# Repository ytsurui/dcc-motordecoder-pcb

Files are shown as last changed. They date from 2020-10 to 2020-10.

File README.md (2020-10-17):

# Atmel ATtiny45 DCC Decoder PCB Data

NMRA規格の信号を受信して作動する、モーター駆動専用のDCCデコーダーのDCCデコーダの基板設計データです。

主にNゲージ鉄道模型への搭載を想定して小型に設計してあります。

主要回路についてはすべてディスクリートで構成してあるため、[回路図](docs/schematic.pdf)を参考にして、ブリッジダイオード、MOSFETなどを適宜大電流に対応可能な部品に差し替えることで、より大型のゲージに対応できるデコーダを構成できるかもしれません。

回路図、基板設計データ、面付け済みの設計データを含みます。
<br>面付け済みのデータについては、ガーバーデータも含みます。 (elecrowにて製造できることを確認済み)

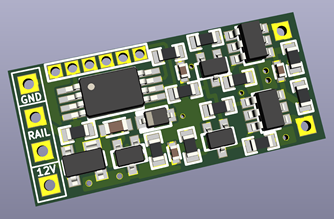
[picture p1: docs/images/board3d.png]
PCB 3D Preview

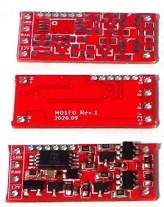
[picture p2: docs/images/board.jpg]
PCB


### 主要スペック
  * 組み立て後の基板サイズ: 22mm x 10mm x 1.7mm
  * 推奨最大電圧: 16V (搭載する鉄道模型車両の最大電圧以下で使用してください)
  * 出力電流: 最大0.5A
  * コンデンサの搭載や、室内灯電源に対応する+12V / GNDのランドを用意
  * マイコン書き込み用端子を用意し、実装後のプログラム書き換えも可能<br>(AVR ISPのピンを1.27mmピッチで1列に伸ばしています)

### 閲覧・編集に必要なCAD (開発環境)
  * KiCad Version (5.1.6)-1 (またはそれ以降)

### 対応するファームウェア
  * [Atmel ATtiny45 DCC Decoder Firmware](https://github.com/ytsurui/dcc-motordecoder-firmware)

### 各種ドキュメント
  * [パーツリスト](docs/partslist.md)

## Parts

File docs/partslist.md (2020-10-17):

# Parts List

<table>
  <tr>
    <td>Reference</td>
    <td>Name</td>
    <td>Package</td>
    <td>Count</td>
    <td>Shop Links</td>
  </tr>
  <tr>
    <td>U1</td>
    <td>ATTiny45-20XUR</td>
    <td>TSSOP-8</td>
    <td>1</td>
    <td><a href="https://www.digikey.jp/product-detail/ja/microchip-technology/ATTINY45-20XUR/ATTINY45-20XURCT-ND/2774364">Digikey (ja)</a><br />
    <a href="https://www.digikey.jp/product-detail/en/microchip-technology/ATTINY45-20XUR/ATTINY45-20XURCT-ND/2774364">Digikey (en)</a></td>
  </tr>
  <tr>
    <td>D1</td>
    <td>BAS3007A-RPP</td>
    <td>SOT-143</td>
    <td>1</td>
    <td><a href="https://www.digikey.jp/product-detail/ja/infineon-technologies/BAS3007ARPPE6327HTSA1/BAS3007ARPPE6327HTSA1CT-ND/2023144">Digikey (ja)</a><br />
    <a href="https://www.digikey.jp/product-detail/en/infineon-technologies/BAS3007ARPPE6327HTSA1/BAS3007ARPPE6327HTSA1CT-ND/2023144">Digikey (en)</a></td>
  </tr>
  <tr>
    <td>D3</td>
    <td>UDZV5.1B</td>
    <td>SOD-323</td>
    <td>1</td>
    <td><a href="https://www.digikey.jp/product-detail/ja/rohm-semiconductor/UDZVTE-175-1B/UDZVTE-175-1BCT-ND/4571455">Digikey (ja)</a><br />
    <a href="https://www.digikey.jp/product-detail/en/rohm-semiconductor/UDZVTE-175-1B/UDZVTE-175-1BCT-ND/4571455">Digikey (en)</a><br />
    <a href="https://akizukidenshi.com/catalog/g/gI-07434/">秋月電子通商</a></td>
  </tr>
  <tr>
    <td>Q1, Q2</td>
    <td>DMG6601LVT<br>DMG6602SVTQ<br>FDC6333</td>
    <td>SOT-23-6</td>
    <td>2</td>
    <td><a href="https://www.digikey.jp/product-detail/ja/diodes-incorporated/DMG6601LVT-7/DMG6601LVT-7DICT-ND/3677910">Digikey, DMG6601LVT (ja)</a><br />
    <a href="https://www.digikey.jp/product-detail/en/diodes-incorporated/DMG6601LVT-7/DMG6601LVT-7DICT-ND/3677910">Digikey, DMG6601LVT (en)</a><br>
    <a href="https://www.digikey.jp/product-detail/ja/diodes-incorporated/DMG6602SVTQ-7/DMG6602SVTQ-7DICT-ND/5176059">Digikey, DMG6602SVTQ (ja)</a><br>
    <a href="https://www.digikey.jp/product-detail/en/diodes-incorporated/DMG6602SVTQ-7/DMG6602SVTQ-7DICT-ND/5176059">Digikey, DMG6602SVTQ (en)</a><br>
    <a href="https://www.digikey.jp/product-detail/ja/on-semiconductor/FDC6333C/FDC6333CCT-ND/965584">Digikey, FDC6333 (ja)</a><br>
    <a href="https://www.digikey.jp/product-detail/en/on-semiconductor/FDC6333C/FDC6333CCT-ND/965584">Digikey, FDC6333 (en)</a>
    </td>
  </tr>
  <tr>
    <td>Q3, Q4, Q5</td>
    <td>2SC4116-GR</td>
    <td>SC-70</td>
    <td>3</td>
    <td><a href="https://www.digikey.jp/product-detail/ja/toshiba-semiconductor-and-storage/2SC4116-GR-LF/2SC4116-GRLFCT-ND/3191333">Digikey (ja)</a><br />
    <a href="https://www.digikey.jp/product-detail/en/toshiba-semiconductor-and-storage/2SC4116-GR-LF/2SC4116-GRLFCT-ND/3191333">Digikey (en)</a><br />
    <a href="https://akizukidenshi.com/catalog/g/gI-02705/">秋月電子通商</a></td>
  </tr>
  <tr>
    <td>C1, C3, C6</td>
	  <td>0.1uF 25V 1005</td>
	  <td>1.0mm x 0.5mm</td>
	  <td>3</td>
    <td><a href="https://www.digikey.jp/product-detail/ja/murata-electronics/GRM155R71H104KE14J/490-13342-1-ND/5973352">Digikey (ja)</a><br />
    <a href="https://www.digikey.jp/product-detail/en/murata-electronics/GRM155R71H104KE14J/490-13342-1-ND/5973352">Digikey (en)</a><br />
    <a href="https://akizukidenshi.com/catalog/g/gP-13377/">秋月電子通商</a></td>
  </tr>
  <tr>
    <td>C2</td>
    <td>22uF 6.3V 1608</td>
    <td>1.6mm x 0.8mm</td>
    <td>1</td>
    <td><a href="https://www.digikey.jp/product-detail/ja/murata-electronics/GRM188R60J226MEA0D/490-7611-1-ND/4280544">Digikey (ja)</a><br />
    <a href="https://www.digikey.jp/product-detail/en/murata-electronics/GRM188R60J226MEA0D/490-7611-1-ND/4280544">Digikey (en)</a><br />
    <a href="https://akizukidenshi.com/catalog/g/gP-08062/">秋月電子通商</a></td>
  </tr>
  <tr>
    <td>R1</td>
    <td>100kohm 1/10W 1608</td>
    <td>1.6mm x 0.8mm</td>
    <td>1</td>
    <td><a href="https://www.digikey.jp/products/ja/resistors/chip-resistor-surface-mount/52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">Digikey (ja)</a><br />
    <a href="https://www.digikey.jp/products/en/resistors/chip-resistor-surface-mount/52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">Digikey (en)</a><br />
    <a href="https://akizukidenshi.com/catalog/g/gR-15321/">秋月電子通商</a></td>
  </tr>
  <tr>
    <td>R2, R3, R6, R7, R10</td>
    <td>1kohm 1/10W 1608</td>
    <td>1.6mm x 0.8mm</td>
    <td>5</td>
    <td><a href="https://www.digikey.jp/products/ja/resistors/chip-resistor-surface-mount/52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">Digikey (ja)</a><br />
    <a href="https://www.digikey.jp/products/en/resistors/chip-resistor-surface-mount/52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">Digikey (en)</a><br />
    <a href="https://akizukidenshi.com/catalog/g/gR-14122/">秋月電子通商</a></td>
  </tr>
  <tr>
    <td>R4, R5</td>
    <td>330ohm 1/10W 1608</td>
    <td>1.6mm x 0.8mm</td>
    <td>2</td>
    <td><a href="https://www.digikey.jp/products/ja/resistors/chip-resistor-surface-mount/52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">Digikey (ja)</a><br />
    <a href="https://www.digikey.jp/products/en/resistors/chip-resistor-surface-mount/52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">Digikey (en)</a><br />
    <a href="https://akizukidenshi.com/catalog/g/gR-06331/">秋月電子通商</a></td>
  </tr>
  <tr>
    <td>R8, R9</td>
    <td>10kohm 1/10W 1608</td>
    <td>1.6mm x 0.8mm</td>
    <td>2</td>
    <td><a href="https://www.digikey.jp/products/ja/resistors/chip-resistor-surface-mount/52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">Digikey (ja)</a><br />
    <a href="https://www.digikey.jp/products/en/resistors/chip-resistor-surface-mount/52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">Digikey (en)</a><br />
    <a href="https://akizukidenshi.com/catalog/g/gR-06103/">秋月電子通商</a></td>
  </tr>
  <tr>
    <td>R11</td>
    <td>4.7kohm 1/10W 1608</td>
    <td>1.6mm x 0.8mm</td>
    <td>1</td>
    <td><a href="https://www.digikey.jp/products/ja/resistors/chip-resistor-surface-mount/52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">Digikey (ja)</a><br />
    <a href="https://www.digikey.jp/products/en/resistors/chip-resistor-surface-mount/52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">Digikey (en)</a><br />
    <a href="https://akizukidenshi.com/catalog/g/gR-14121/">秋月電子通商</a></td>
  </tr>
</table>

---

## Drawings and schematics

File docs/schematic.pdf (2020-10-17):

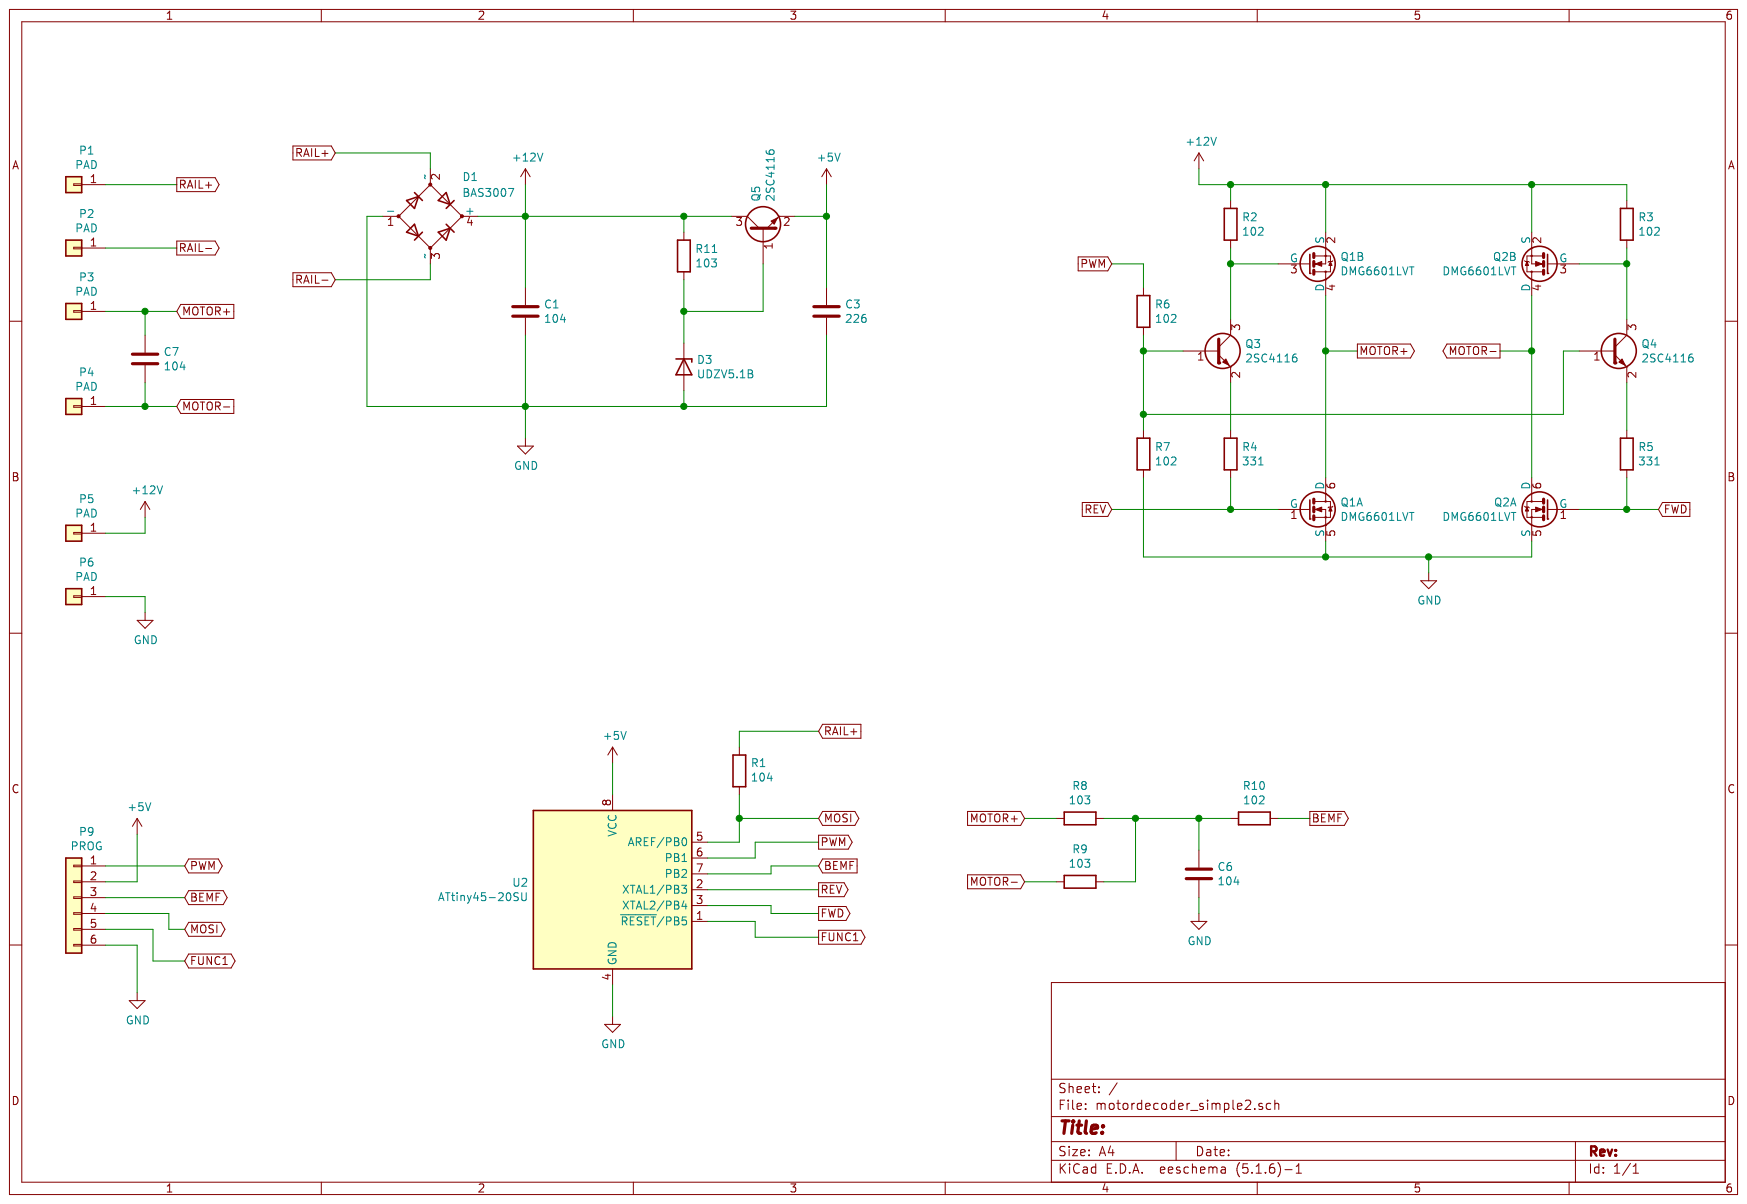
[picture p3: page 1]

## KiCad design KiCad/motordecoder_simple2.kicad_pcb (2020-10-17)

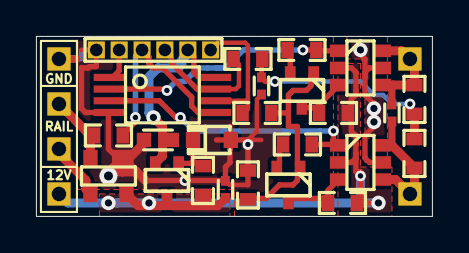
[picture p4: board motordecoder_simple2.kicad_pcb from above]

Board: 2 copper layers, 22.0 x 10.0 mm, 30 parts (0 on the bottom side), 20 nets.

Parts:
C1, C6, C7: 104; C_1005
C3: 226; C_1608
D1: BAS3007; SOT-143
D3: UDZV5.1B; UMD2
P1, P2, P3, P4, P5, P6: PAD; PAD_1.3x1.3_Hole0.8
P9: PROG; PAD_PROG_6PIN_HOLE0.7
Q1, Q2: DMG6601LVT; SOT-23-6
Q3, Q4, Q5: 2SC4116; SC-70
R1: 104; R_1608
R2, R3, R6, R7, R10: 102; R_1608
R4, R5: 331; R_1608
R8, R9, R11: 103; R_1608
U2: ATtiny45-20SU; TSSOP-8

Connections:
+5V: C3.1, P9.2, Q5.2, U2.8
+12V: C1.1, D1.4, P5.1, Q1.2, Q2.2, Q5.3, R2.1, R3.1, R11.1
BEMF: P9.3, R10.1, U2.7
FUNC1: P9.5, U2.1
FWD: Q2.1, R5.2, U2.3
GND: C1.2, C3.2, C6.2, D1.1, D3.2, P6.1, P9.6, Q1.5, Q2.5, R7.2, U2.4
MOSI: P9.4, R1.1, U2.5
MOTOR+: C7.1, P3.1, Q1.4, Q1.6, R8.2
MOTOR-: C7.2, P4.1, Q2.4, Q2.6, R9.2
unnamed: C6.1, R8.1, R9.1, R10.2
unnamed: D3.1, Q5.1, R11.2
unnamed: Q1.3, Q3.3, R2.2
unnamed: Q2.3, Q4.3, R3.2
unnamed: Q3.1, Q4.1, R6.2, R7.1
unnamed: Q3.2, R4.1
unnamed: Q4.2, R5.1
PWM: P9.1, R6.1, U2.6
RAIL+: D1.2, P1.1, R1.2
RAIL-: D1.3, P2.1
REV: Q1.1, R4.2, U2.2
